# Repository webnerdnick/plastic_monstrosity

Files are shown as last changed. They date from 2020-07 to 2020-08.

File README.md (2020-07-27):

# Plastic Monstrosity
## 3D Printable 4' x 8' CNC machine

The printable part files are originally sourced from spiffcow's git repo, and details and documentation have been compied from the Thingiverse project page at: https://www.thingiverse.com/thing:2471313 and OpenBuilds here: https://openbuilds.com/builds/plastic-monstrosity.5353/

This repo was started as a way to further organize the project and make it easier for those wishing to build the project to understand how things come together. 

If you'd like to contact me with questions or contibuting, please feel free to contact me at webnerdnick@gmail.com.

### Original Summary of Project
> This is my massive CNC capable of cutting a full 4x8 sheet of plywood with room to spare! This is optimized specifically for cutting plywood, and I believe this is probably the least expensive way to build a CNC capable of accurately cutting plywood in a reasonable amount of time. There are other designs out there, but I've yet to see another one that maintains performance and accuracy while keeping the overall price below $1000 for a 4x8' cutting area. I really enjoyed designing and building this, and I hope it can help lower the barrier of entry for makers looking to build the kind of things you see on [OpenDesk](http://www.opendesk.cc) or [WikiHouse](https://wikihouse.cc/).

In a nutshell, this project uses 3D printable parts, tons of nuts and bolts, bearings, and some off the shelf parts from Open Builds, and 2" EMT conduit (or 60.3mmm conduit for European folks) for the long axis. For a complete listing of parts, please visit the BOM below.

While the short axis is primarily determined by the length of the C-Beam you purchase from OpenBuilds, the long axis can be nearly any length, if space is limited.

# Contents
[Bill of Materials](bom.md)

[Spindle Options](spindles.md)

[Print Settings](print_settings.md)

[Building the Table](building_bench.md)

[Adding the long-axis Rails (using the jig.stl)](adding_rails.md)

[Possible Upgrades](upgrades.md)

[FAQ](faq.md)

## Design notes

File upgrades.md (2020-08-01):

# Possible Upgrades

## OpenBuilds Short Axis Gantry Mount

The following upgrades will replace the 3D printed parts with machined plates and parts from OpenBuilds. This would allow for a much more rigid setup for attaching spindles, increasing overall accuracy.

This aassumes that you've already purchased the C-Beams, motor, and threaded rod for the z-axis, and have printed the endcap.stl, guardplate.stl, and the bottomEndcap.stl files.

*There are several nuts, bolts, and shims that need to be identified and added to the BOM below.*

| Qty. | Part | Price Ea. | Link |
|---|---|---|---|
| 2 | XLarge C Beam Gantry Plate | $14.99  | https://openbuildspartstore.com/xlarge |
| 1 | C-Beam Gantry Plate | $9.99 | https://openbuildspartstore.com/c-beam-gantry-plate/ |
| 1 | Motor Mount Plate - NEMA 23 | $7.99 | https://openbuildspartstore.com/motor-mount-plate-nema-23-stepper-motor/ |
| 8 | Solid V Wheel Kit * | $6.99 | https://openbuildspartstore.com/xtreme-solid-v-wheel-kit/ |
| 4 | 6mm Eccentric Spacer | $1.99 | https://openbuildspartstore.com/eccentric-spacer/ |

*Note: Requires Solid V Wheel kit, instead of Mini V Wheel kit for the gantry. 4 mini v wheels are still used for the z-axis plate.

Eccentric spacers should only be needed on the top side of the gantry in order to snug up the wheels.

From thingiverse, user Luk14, gave these overview pictures of his upgraded gantry, using the BOM above.

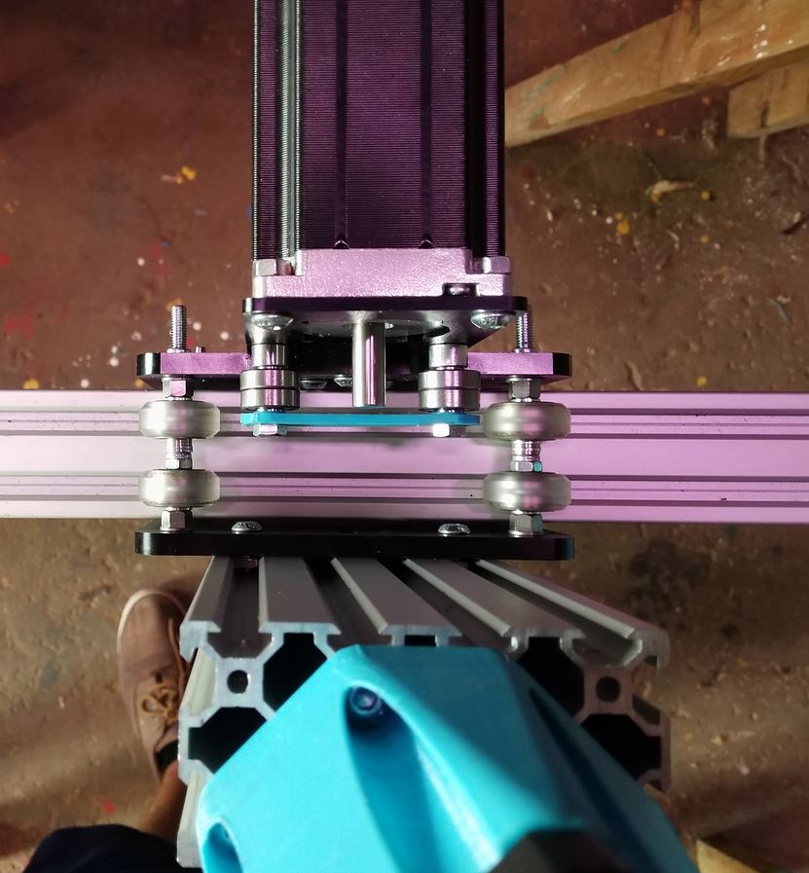
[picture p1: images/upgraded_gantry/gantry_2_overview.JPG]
upgraded gantry overview


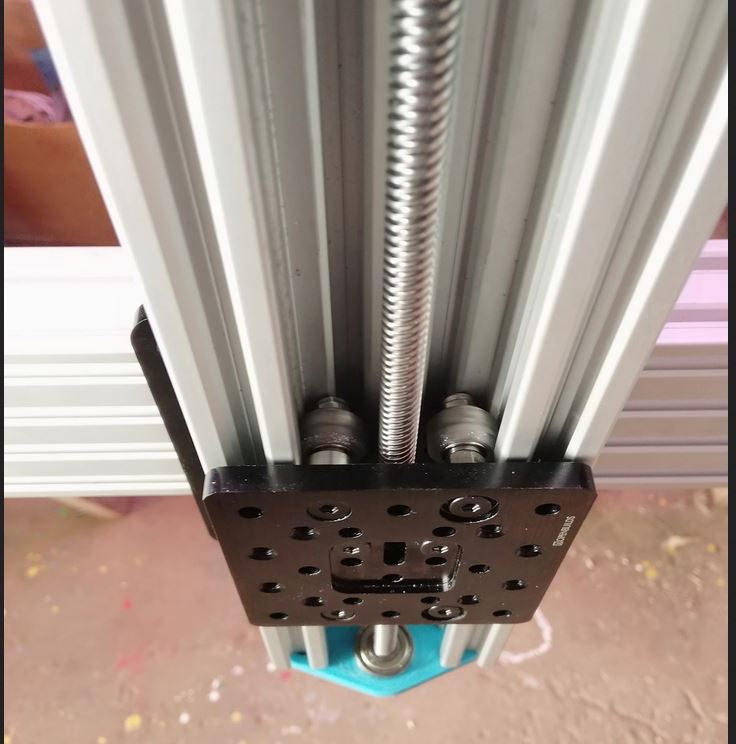
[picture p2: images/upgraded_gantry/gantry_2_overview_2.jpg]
upgraded gantry overview 2


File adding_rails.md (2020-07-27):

# Using to Jig to add rails to the workbench

Figure out how you're going to attach the conduit stand-offs to the condut. I'm using self-tapping screws, but I'll drill pilot hole in the conduit first using the jigs.  You can also get an M5 tap and a 4.5mm drill bit and make threaded holes. It's up to you, but before you do any drilling, figure out what you're going to attach the stand-offs with. You'll need something threaded so you can slightly adjust the stand-offs as you attach them at the end.

# Step 1
* Purchase two 10 foot pieces of 2" EMT conduit. It's metallic thin-wall conduit, and should be about 2-3/16" OD.
* Print 2 of the jig.stl files
    * Print using 20% infill out of PLA or something similar. These won't be used as part of the actual CNC machine, so it's ok to skimp here

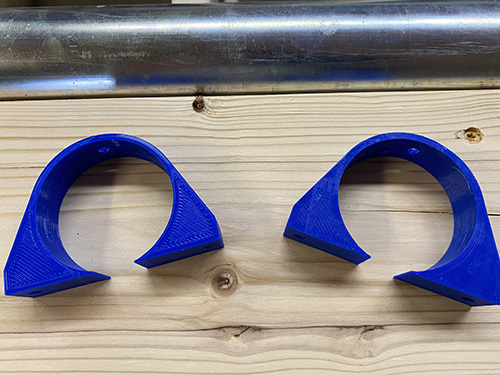
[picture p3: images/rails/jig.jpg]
jig templates


# Step 2
Using the jig, mark a line at 9' on the conduit, and cut at that length, it'll give you a nice line to follow when cutting with a hack saw or sawz-all

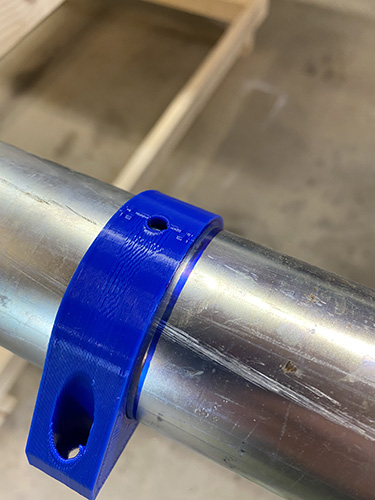
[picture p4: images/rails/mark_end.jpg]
marking the end


# Step 3
Using a file or sand paper, clean up the ends of the pipe, they'll be sharp

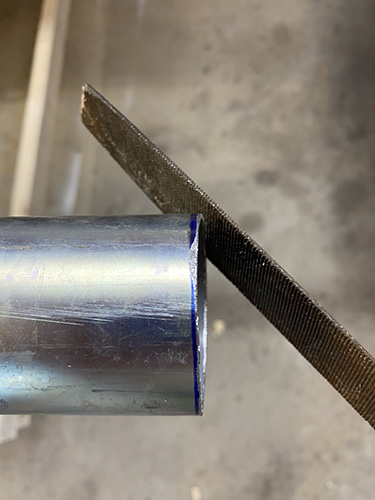
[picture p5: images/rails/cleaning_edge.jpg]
clean the end of the pipe


# Step 4
Most likely, you're conduit will have a slight bend along the length. Using a board with a flat edge, find the crown on the pipe by slowly rotating the pipe against the board. Note the opposite of the pipe where you have the greatest gap when laying up against the board.  This way when attaching your clips to the conduit, the can be parallel to the bend and make it easier to pull the bend out of the pipe as you screw it down to the workbench.

Here you can see this side of the pipe doesn't have a bend in it

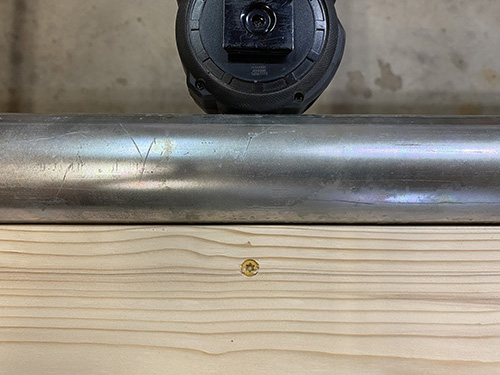
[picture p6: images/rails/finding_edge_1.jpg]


As I continued to rotate the pipe, this shows the crown, and I marked the opposite side

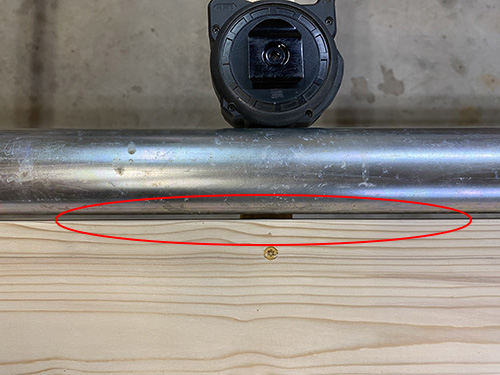
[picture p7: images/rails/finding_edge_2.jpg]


Here I marked 180 deg. from where the bend was the greatest against the straight edge. This point will become the side that I want to install the conduit mounts on.

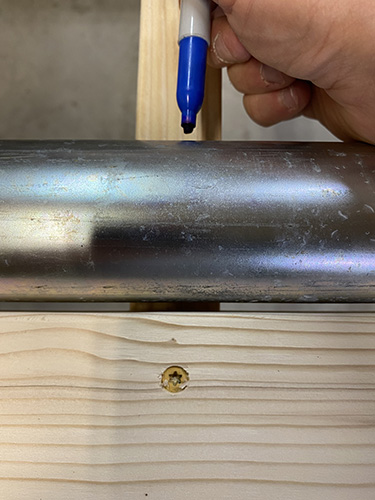
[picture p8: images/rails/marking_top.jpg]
making opposite side of bend


# Step 5
Let's put the jigs to use. Figure out how often you want to space the conduit stand-offs on the piece of pipe, you'll need to know that for buidling the jig.  I chose to space my stand-offs around 21".

On your flat board that you'll attach the jigs to, measure the distance you want to space the jigs and make a mark on the board.  

Slide your jigs over the conduit, and place them on the marks you made on the board.  Right now, spacing on the pipe itself it's important, we're just focusing on attaching the jigs to the board, and the pipe is there to make sure they are lighed up properly. Screw the jigs down to the board at the spacing you set.  One side can be screwed down tight, but leave a few turns left when you screw down the other side of the jig. This will allow the pipe to slide.

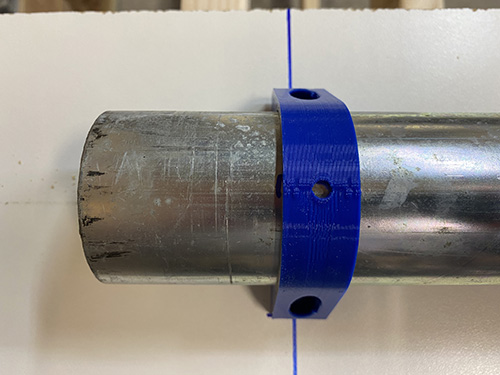
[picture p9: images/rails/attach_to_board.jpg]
space the rails


# Step 6
I left 2" at the end of the pipe before drilling a hole for the first conduit stand-off. You'll need to leave yourself some space for the long-axis belt mount.

Rotate your pipe, so the mark you made on the crown is up.

Mark or drill the first hole in the conduit using the top hole in the jig.

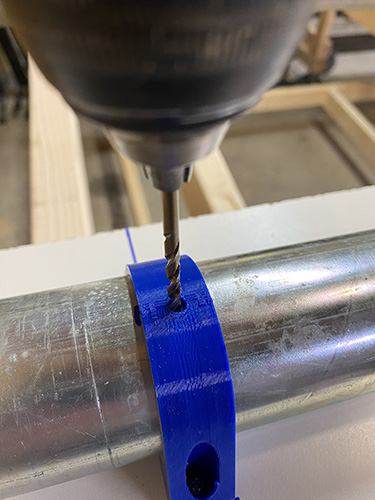
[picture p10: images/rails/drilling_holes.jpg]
drill holes


# Step 7
After drilling one hole, place a screw, bolt, or spare drill bit into the hole, so the pipe doesn't move, and drill the second hole using the other jig.

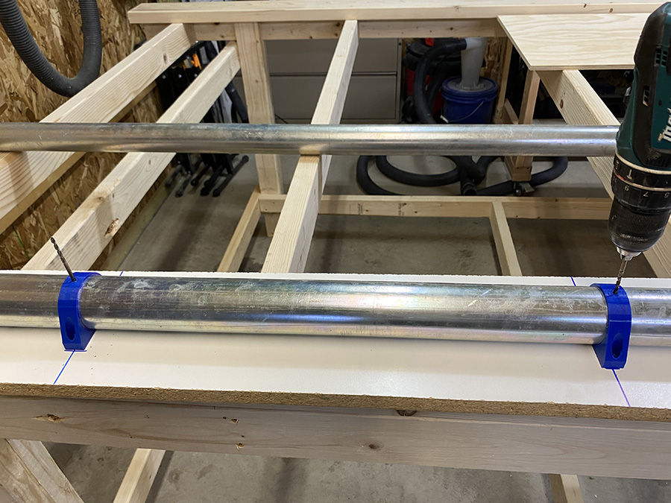
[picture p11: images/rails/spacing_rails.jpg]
drill 2nd hole


# Step 8
Once you drill the 2nd hole, remove the drill bit in the first hole, and slide the pipe down through the jigs so that the 2nd hole now lines up with the hole in the first jig, and put another drill bit or something in that hole to keep the pipe from turning.  

Now drill another hole using the 2nd jig.

Repeat until you reach the end of the pipe.

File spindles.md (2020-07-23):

# Spindle Options

Depending on the rigidity of the short-axis gantry, your options could almost be limitless. However, with 3D printed parts, the following options are recommended.

## Makita RT0701c 1-1/4 HP Compact Router

* 1/4" Collet
* Broad RPM range or 10,000 to 30,000 RPM
* Easy to replace brushes and bearings
* About 4 lbs
* Around $99 on [Amazon](https://www.amazon.com/gp/product/B00E7D3V4S)

*Use the makita.stl part to hold this spindle*

## Dewalt DWP611 1-1/4 HP Router
* 1/4" Collet
* 16,000 - 27,000 RPM
* LED Work Light
* About 5 lbs
* Around $139.00 on [Amazon](https://www.amazon.com/gp/product/B0048EFUV8)

*Use the dwp611.stl to hold this spindle*

## Carbide Compact Router
* 110 V AC only with US Plug
* 1/4" Collet
* 12,000 - 30,000 RPM
* Rebranded Makita
* 14 foot power cord
* comes with 2 sets of replacement brushes
* $80 at [Carbide3D](https://shop.carbide3d.com/products/carbide-compact-router?variant=14063567667261)

*Use the zAxis_65mm_spindle.stl to hold this spindle*

## Generic Options

52mm, 70mm, and 80mm generic spindle mounts are also included in the printable parts, for a range of other available spindles. I do not have any specific experience or recomendations for a generic spindle.

*Use zAxis-52mm-spindle.stl, zAxis-70mm-spindle.stl, or zAxis-80mm-spindle.stl

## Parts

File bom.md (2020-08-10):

# Bill of Materials

I'm doing my best to provide a complete bill of materials with complete sources. During certain times, specifically linked items may be out of stock, but as long as you substitute with an equivalent item, you should be ok. I am continually updating this list.

All sources and prices below are accurate of 7/23/2020, prices and availability may fluctute. All sources are for USA shipping.  

*If anyone would like to research and provide me with reasonable substitutions or links for other countries, please reach out to me.*

## Electronics

| Qty.  | Item | Price Ea.  | Site | Link | Comments |
| ----- | --- | --- | --- | -----| --- |
| 1 | MKS Sbase Board | $53.99 | Amazon | https://www.amazon.com/gp/product/B071X8MBYT/ref=crt_ewc_img_dp_3?ie=UTF8&psc=1&smid=A2K1WYI5NZ8QSW | Main controller board|
| 1 | 24V DC 15A 360W PSU | $18.98 | Amazon | https://www.amazon.com/gp/product/B0146IAXYO/ref=crt_ewc_img_dp_4?ie=UTF8&psc=1&smid=AMNTPWSAB5H0S | Primary PSU|
| 3 | NEMA 23 Stepper Motor 269 oz/in, 76cm, **8mm bore** | $28.00 | Amazon | https://www.amazon.com/gp/product/B07Y81FF3V/ref=crt_ewc_img_dp_2?ie=UTF8&psc=1&smid=A1AY59LT54ZBYI | Long and Short Axis Motors |
| 1 | NEMA 17 Stepper Motor, 84 oz/in 48mm body | $13.99 | Amazon | https://www.amazon.com/gp/product/B00PNEQKC0/ref=crt_ewc_title_dp_7?ie=UTF8&psc=1&smid=AWQBCGWISS7BL | z-axis motor |
| 1 | 100 ft 18/4 stranded wire ** | $28.78 | Amazon | https://www.amazon.com/gp/product/B01KWBPC6S/ref=crt_ewc_title_dp_2?ie=UTF8&psc=1&smid=A23GDHUTXWRYW4 | |
| 1 | JST SM Connectors (600qty male/female) ** | $15.99 | Amazon | https://www.amazon.com/gp/product/B074LVGVTY/ref=crt_ewc_title_huc_3?ie=UTF8&psc=1&smid=A6QA7SV6MW7GH | For connecting steppers to CPU|

***You're not going to need all 600 of these connectors, you'll only need a handful to make extension cables for the stepper motors
to connect to the controller board. The stepper motors DO NOT come with plugs or long cables.

Also, 18 AWG wire is the smallest wire recommended (bigger the number, smaller the wire dia.), make sure you're purchasing stranded wire as well*

## Rails and Conduit

| Qty.  | Item | Price Ea.  | Site | Link | Comments |
| ----- | --- | --- | --- | -----| --- |
| 2 | 2" EMT (thin wall) electrical conduit. NOT PVC  | $26.99 | Ace Hardware | | Outside dia. is 2-3/16"|
| 1 | C-Beam Linear Rail, 1500mm (59") | $47.99 | Open Builds | https://openbuildspartstore.com/c-beam-linear-rail/ | Short Axis|
| 1 | C-Beam Linear Rail, 250mm (9.8") | $8.99 | Open Builds | https://openbuildspartstore.com/c-beam-linear-rail/ | z-axis |

# Moving Things

| Qty.  | Item | Price Ea.  | Site | Link | Comments |
| ----- | --- | --- | --- | -----| --- |
| 2 | 5 meter Timing Belt, 10mm Wide, 2mm Pitch | $13.98 | Amazon | https://www.amazon.com/gp/product/B078STSGSX/ref=crt_ewc_img_dp_8?ie=UTF8&psc=1&smid=A3CUHW0VYGYSCN |  long and short axis|
| 1 | 300 mm T8 Lead Screw, 2mm pitch, 2 start 4mm lead | $9.99 | Amazon | https://www.amazon.com/gp/product/B07ZC741KB/ref=ppx_yo_dt_b_asin_title_o00_s00?ie=UTF8&psc=1 | z-axis|
| 1 | 5 pack 2GT-20 Timing Pulley, 20 teeth, 10mm width, 8mm bore ** | $10.99 | Amazon |  https://www.amazon.com/gp/product/B079JMHZW7/ref=crt_ewc_img_srh_1?ie=UTF8&psc=1&smid=A31QZVWR40HWH8 ||
| 1 | 4 pack 5mm to 8mm leadscrew coupler | $6.99 | Amazon | https://www.amazon.com/KINGPRINT-Coupling-Accessories-Engraving-Machines/dp/B073FDXHMG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 | coupling z-axis motor to leadscrew |
| 1 | 20 pack 625-zz bearing (5mm x 16mm x 5mm) | $9.95 | eBay | https://www.ebay.com/itm/625-ZZ-C3-Premium-Metal-Shielded-Ball-Bearing-5x16x5-625Z-20-QTY/303360064601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 | |
| 1 | 2- Pack 608-zz bearings (8mm x 22mm x 7mm) | $8.99 | Amazon | https://www.amazon.com/gp/product/B07211VH78/ ||
| 12 | Xtreme Mini V Wheel Kit *** | $5.99 | Open Builds | https://openbuildspartstore.com/xtreme-mini-v-wheel-kit/ | short and z-axis wheels |

***The bore must match whatever shaft diameter is on your NEMA 23 motors. The more popular 6.35mm x 10mm wide pulleys were impossible to find, so I changed out my steppers to an 8mm bore, along with these pulleys.  Pay careful attention to the specs of the pulley. 20 teeth, 10mm wide.
****If you plan to use the upgrade of the Open Builds short axis gantry, you only need 4 Xtreme Mini V Wheels instead of 12, as you'll then need 8 Solid V wheels. (See [upgrades](upgrades.md) for BOM)*

# Nuts and Bolts

Out of convenience and better pricing, large packs of nuts and bolts are linked, though you may not need 50 of one thing, it'll still be cheaper than having to buy 30 at a local store. YMMV. I've tried to actualy list how many of each you'll actually use in case you want to get them locally.

*Note: Consider stainless steel or zinc options if your CNC machine will be exposed to humidity or stored in a garage or shed*

| Qty.  | Item | # Used | Price Ea.  | Site | Link | Comments |
| ----- | --- | ---|--- | --- | -----| --- |
| 1 | Anti-Backlash Nut, 8mm T8, 4mm Lead | 1 | $8.88 | Amazon | https://www.amazon.com/gp/product/B07T2MYS6D/ref=crt_ewc_title_dp_5?ie=UTF8&psc=1&smid=A3C0HXP4AGBIOG | |
| 1 | 100 pack m5 lock nut 0.80 thread | | $8.94 | eBay | https://www.ebay.com/itm/Stainless-Steel-Nylon-Insert-Hex-Lock-Nut-M2-5-M3-M4-M5-M6-M8-M10-M12-DIN-985/122599345751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 | |
| 1 | 50 pack m5 THIN jam nuts, 0.80 thread | | $13.99 | eBay | https://www.ebay.com/itm/Metric-DIN-439B-Jam-Nuts-Zinc-Plated-Steel-Class-04-Jam-Thin-Hex-Nuts-M4-M36/401806123372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 | |
| 3 | 50 pack 20 series m5 Tee Nut, Slide-In  ** | | $8.99 | Amazon | https://www.amazon.com/gp/product/B07MHH1HFQ | |
| 1 | 20 pack m5 75mm cap head bolt | | $9.61 | eBay | https://www.ebay.com/itm/M5-Socket-Head-Cap-Screws-12-9-Alloy-Steel-w-Black-Oxide-DIN-912-0-80-Coarse/112016494139 | |
| 1 | 50 pack m5 30mm cap head bolt | | $9.30 | eBay | https://www.ebay.com/itm/M5-Socket-Head-Cap-Screws-12-9-Alloy-Steel-w-Black-Oxide-DIN-912-0-80-Coarse/112016494139 | |
| 1 | 50 pack m5 25mm cap head bolt | | $8.45 | eBay | https://www.ebay.com/itm/M5-Socket-Head-Cap-Screws-12-9-Alloy-Steel-w-Black-Oxide-DIN-912-0-80-Coarse/112016494139 | |
| 1 | 100 pack m5 12mm cap head bolt | | $11.72 | eBay | https://www.ebay.com/itm/M5-Socket-Head-Cap-Screws-12-9-Alloy-Steel-w-Black-Oxide-DIN-912-0-80-Coarse/112016494139 | |
| 20 | 5/16"-18 lock nuts (nylon) | | $0.15 | Ace Hardware | | used on long axis |
| 4 | 5/16"-18 Hex bolt 2" long | | | Ace Hardware | | long axis, center bearings |
| 10 | 5/16"-18 hex bolt 3.5" long  ****** | | $0.45 | Ace Hardware | | used on long axis | 
| 20 | 5/16"-18 hex bolts 1.5" long | | $0.25 | Ace Hardware | | long axis, side bearings |

***You want slide-in, NOT drop-in tee nuts. The drop in are a pain to work with, but make sure you have the right amount of nuts in the slot before assembling or you'll have to take it apart to add a nut*

*******These may not be needed, currently in review.*

# Cutting Things 
| Qty.  | Item | Price Ea.  | Site | Link | Comments |
| ----- | --- | --- | --- | -----| --- |
| | Makita Compact Router | $99.00 | Amazon | https://www.amazon.com/gp/product/B00E7D3V4S | |
|  OR  | |||||
| | DeWalt DWP611 Router | $139.00 | Amazon | https://www.amazon.com/gp/product/B0048EFUV8 | |
| | | | | | |
| 1 | 1/4" Up-Cut Solid Carbide Spiral Bit ** | $19.53 | Amazon | https://www.amazon.com/gp/product/B000K2BGNS | |

***Lowes also carries these, but they are about $2-$3 more expensive than Amazon.*

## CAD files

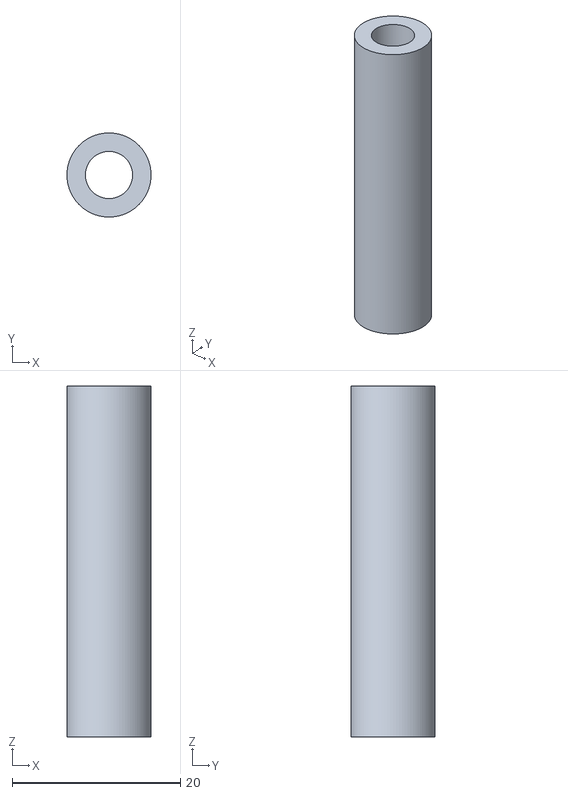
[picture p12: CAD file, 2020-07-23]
part_files/shortAxisFullLengthSpacer.stl
10.0 x 9.99 x 41.7

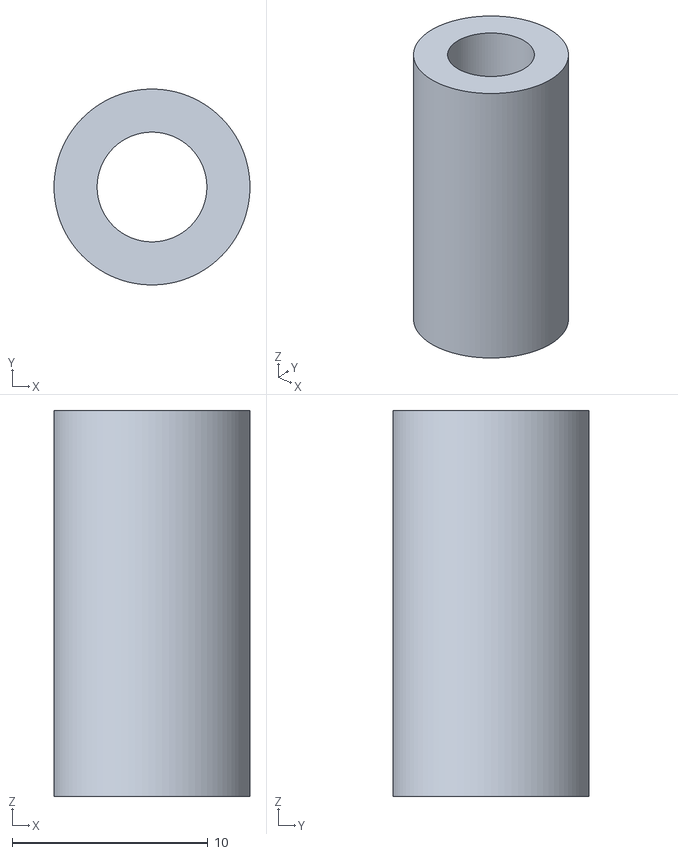
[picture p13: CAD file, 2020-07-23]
part_files/official/longAxisFullLengthSpacer.stl
10.0 x 9.99 x 19.7

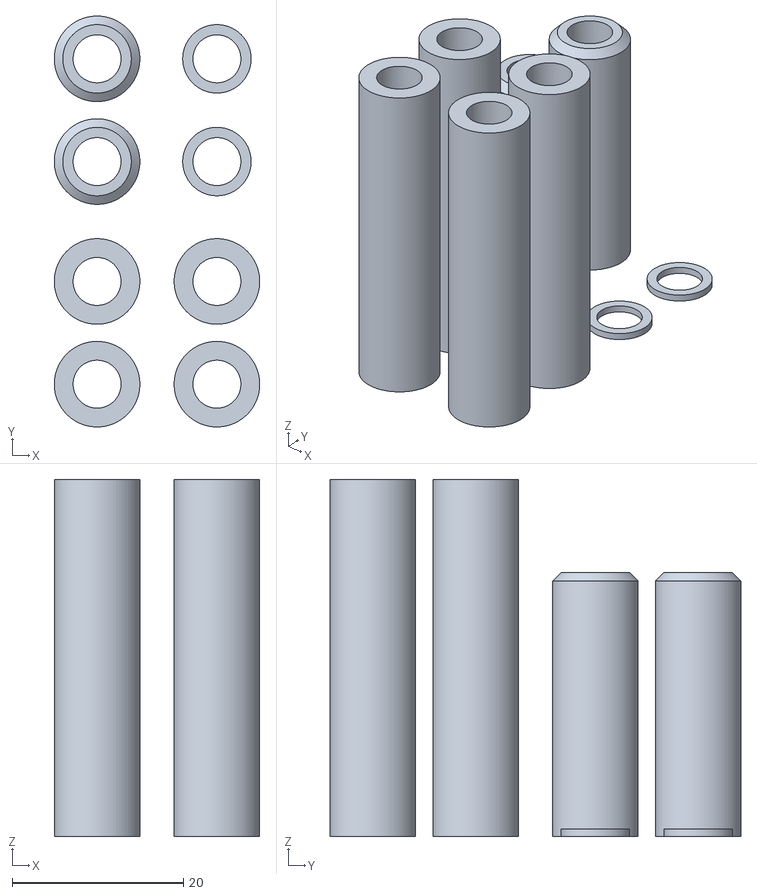
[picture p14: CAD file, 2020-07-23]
part_files/official/2017-08-07/shortAxisSpacers.stl
24.0 x 48.0 x 41.7

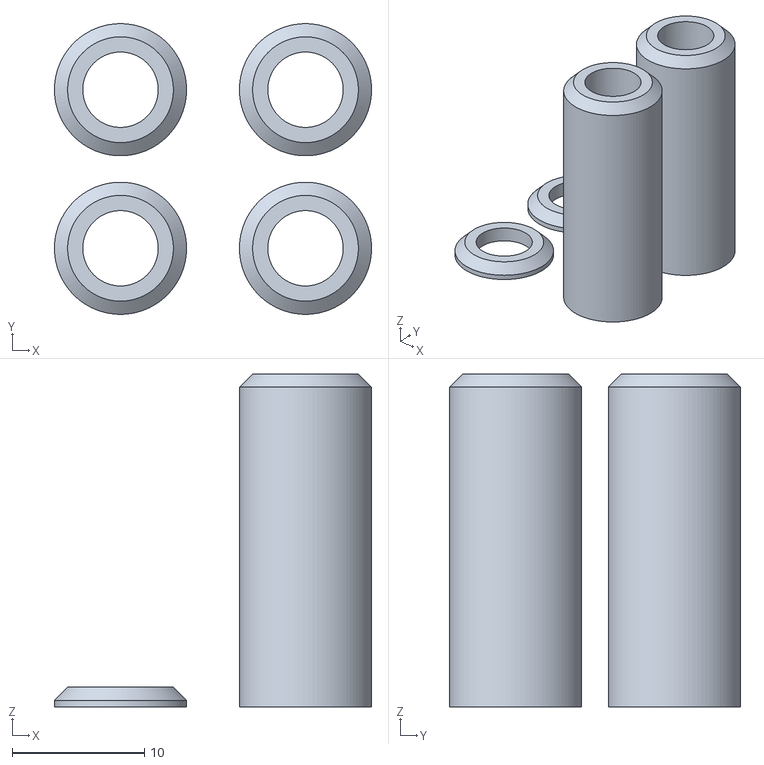
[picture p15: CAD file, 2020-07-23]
part_files/official/2017-08-09/shortAxisSpacers_bearingonly_shortMotorShaft.stl
24.0 x 22.0 x 25.2

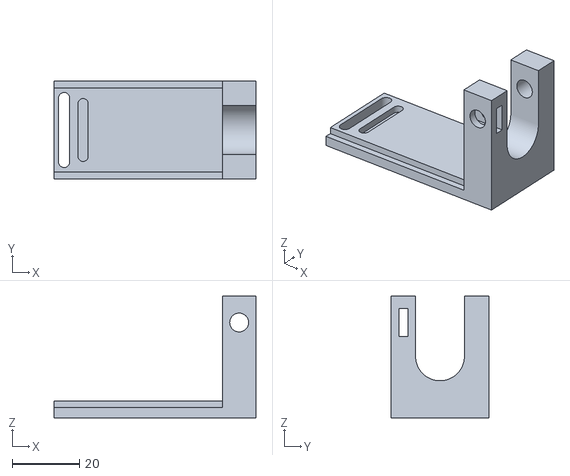
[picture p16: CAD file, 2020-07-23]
part_files/official/2017-08-16/probeHolder.stl
60.0 x 29.0 x 36.1

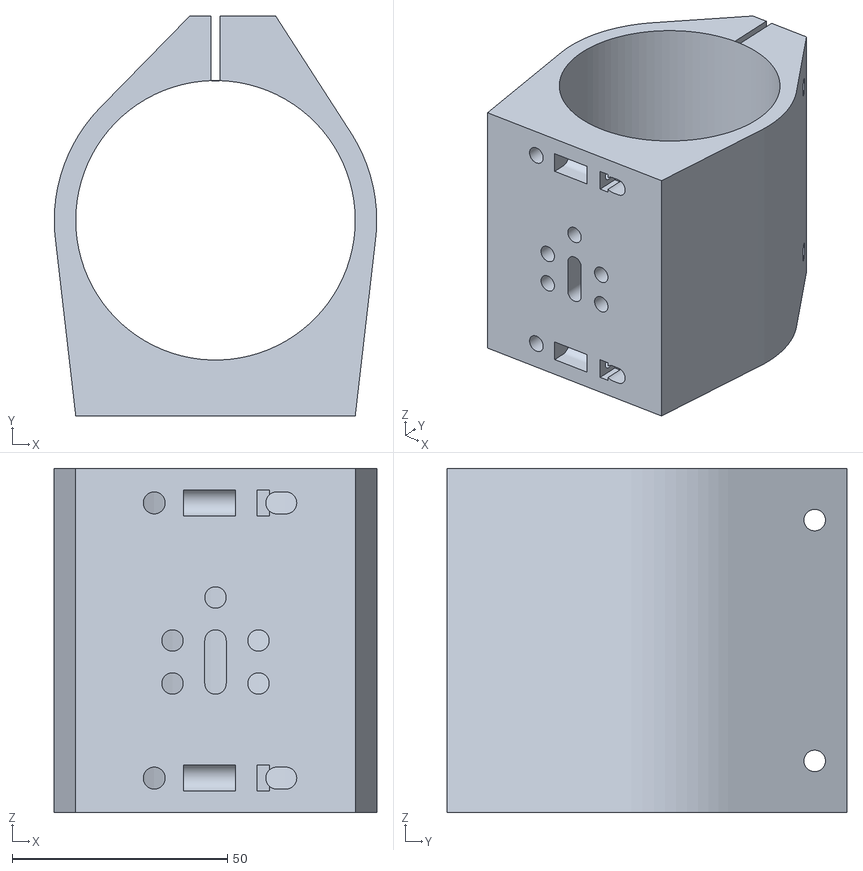
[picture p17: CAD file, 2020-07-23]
part_files/official/2017-08-22/makita.stl
75.0 x 93.0 x 80.0

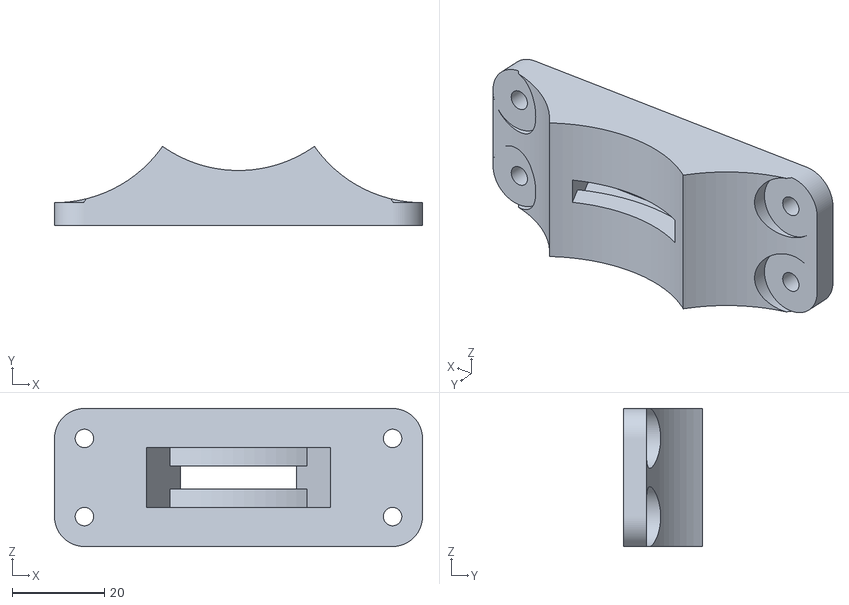
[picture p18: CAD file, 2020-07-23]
part_files/official/2017-09-20/ConduitUndersideBase_60.3mm.stl
80.0 x 17.3 x 30.0

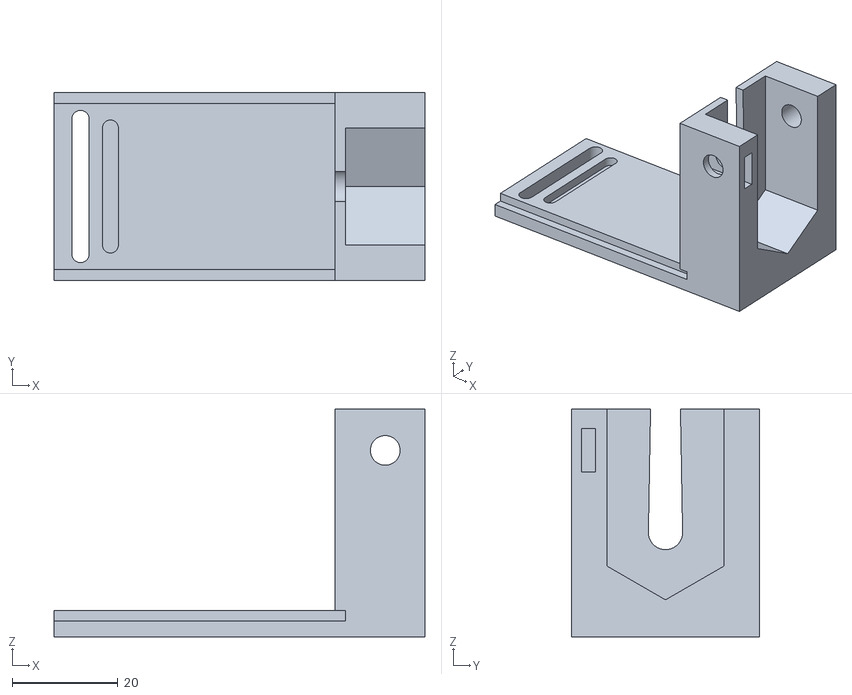
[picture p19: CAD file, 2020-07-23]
part_files/official/2017-10-05/probeHolder-Makita.stl
70.0 x 35.4 x 43.0

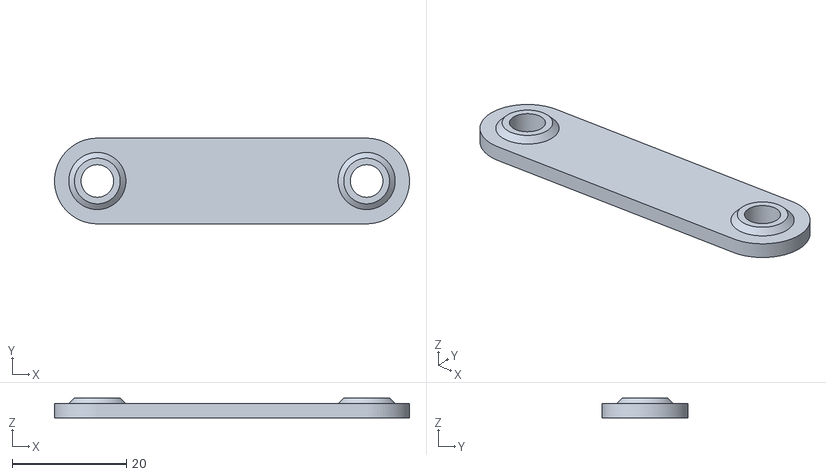
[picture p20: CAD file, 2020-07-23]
part_files/official/2017-11-02/guardPlate.stl
62.1 x 15.0 x 3.50

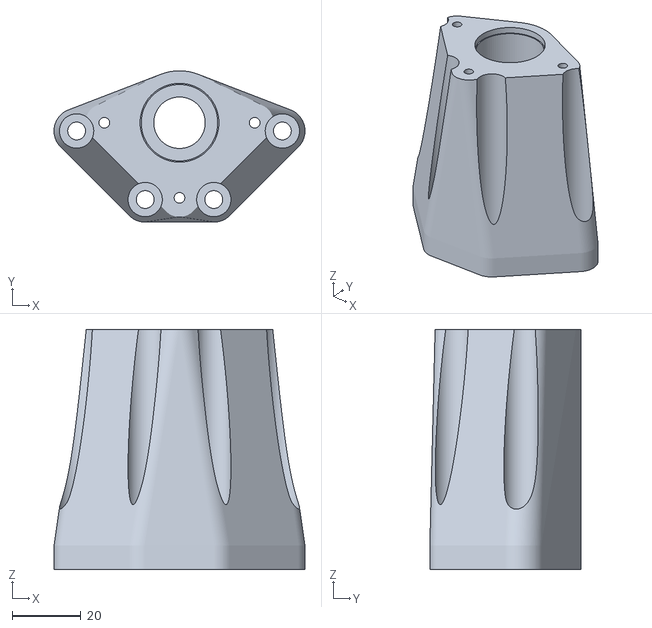
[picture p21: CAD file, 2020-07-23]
part_files/official/2017-12-03/endcap.stl
73.2 x 44.1 x 70.0

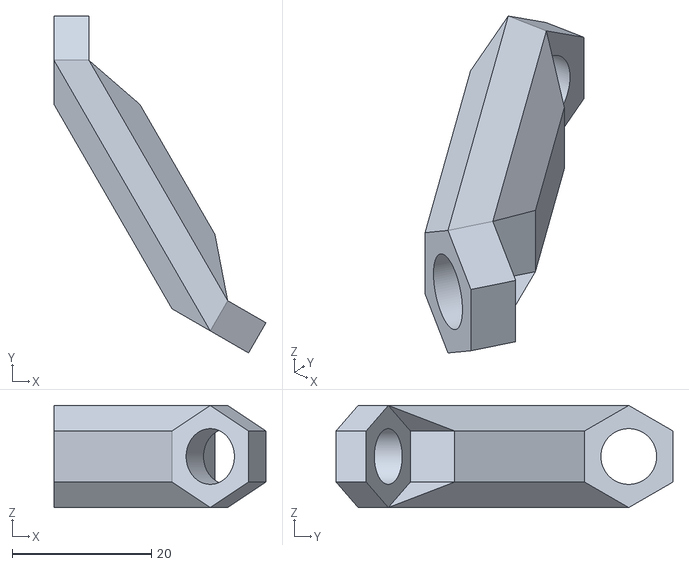
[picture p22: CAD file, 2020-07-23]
part_files/official/brace.stl
30.4 x 48.4 x 14.7

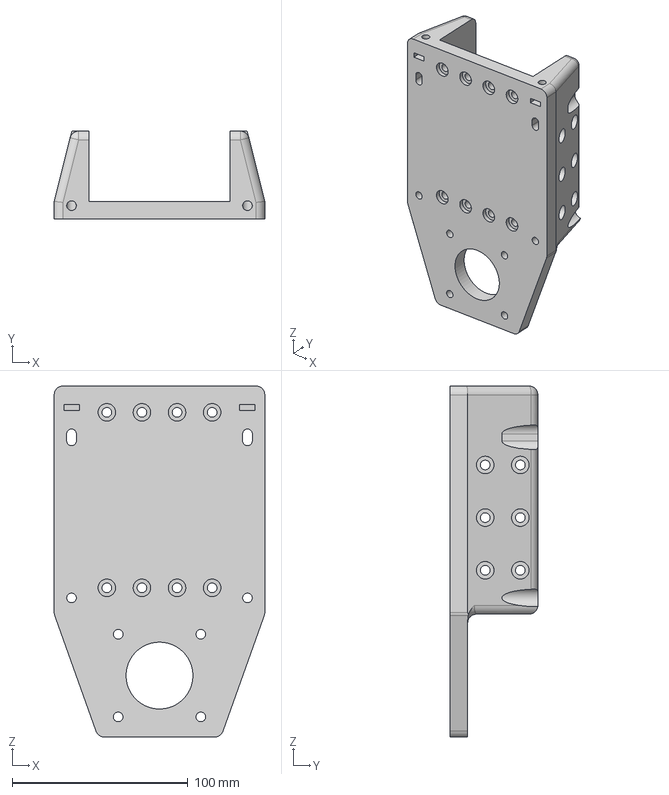
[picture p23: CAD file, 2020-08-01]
part_files/redesigned/shortAxisPlateFront.step
120.0 x 50.0 x 200.0 mm

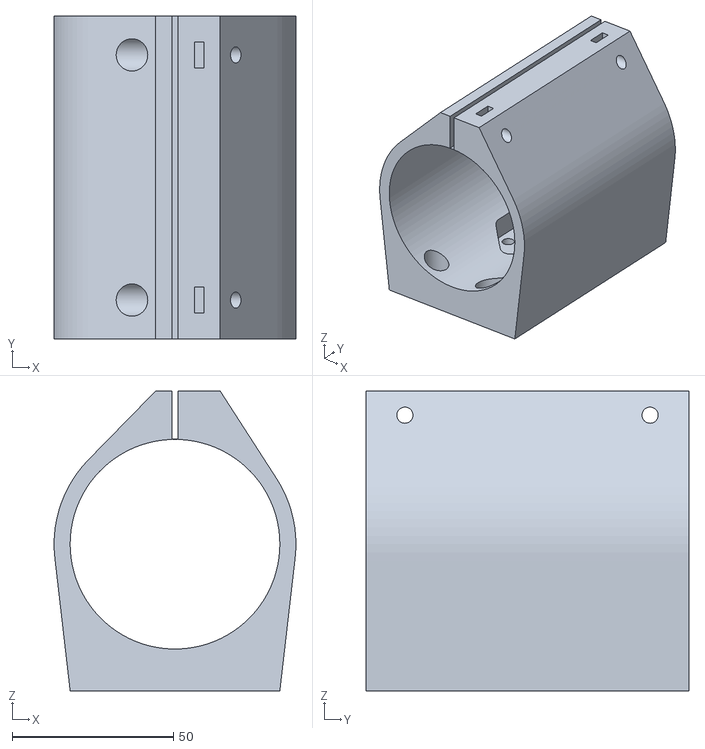
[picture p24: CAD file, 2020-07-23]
part_files/zAxis_65mm_spindle.stl
75.0 x 100.0 x 93.0

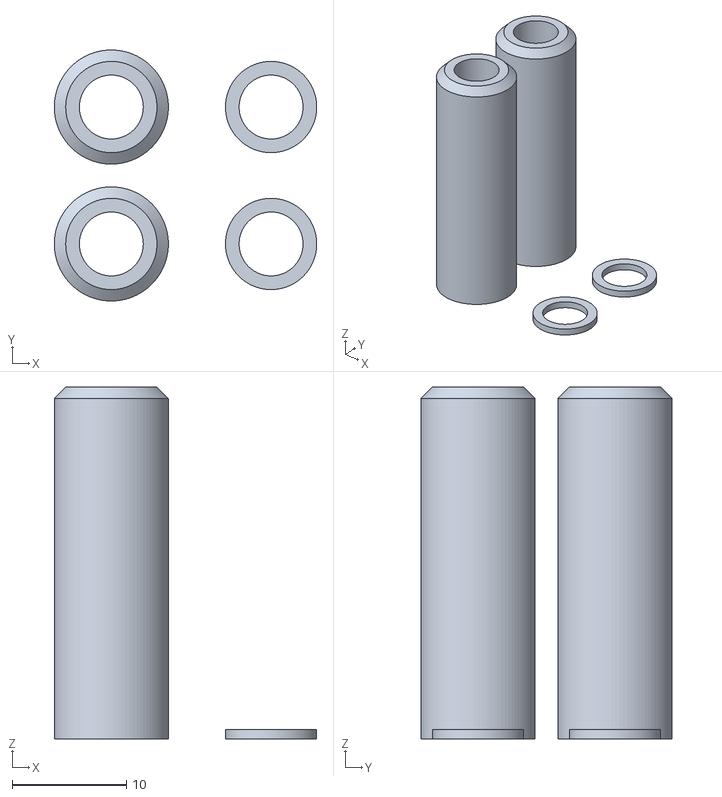
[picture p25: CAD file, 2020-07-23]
part_files/official/2017-08-07/shortAxisSpacers_bearingonly.stl
23.0 x 22.0 x 30.9

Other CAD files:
part_files/official/2017-08-09/beltMountShortAxis_shortMotorShaft.stl
part_files/official/2017-08-22/dwp611.stl
part_files/constants.scad
part_files/beltMount.scad
part_files/beltMount_60.3mm.scad
part_files/beltMountShortAxis.scad
part_files/20mm_spacer.stl
part_files/625Spacer.stl
part_files/6mm_spacer.stl
part_files/Carriage.scad
part_files/Carriage2.scad
part_files/Carriage3.scad
part_files/Carriage3_20.4mm.scad
part_files/Carriage3_60.3mm.scad
part_files/Carriage3_test.stl
part_files/Carriage4.scad
part_files/UAE8-to-5mm.scad
part_files/UAE8-to-5mm.stl
part_files/beltMount.stl
part_files/beltMountShortAxis.stl
part_files/beltMountShortAxis_shortShaft.scad
part_files/beltMountShortAxis_shortShaft2.scad
part_files/beltMountShortAxis_shortShaft3.scad
part_files/bottomEndcap.stl
part_files/brace.scad
part_files/carriageSpacer.stl
part_files/connector.scad
part_files/connector.stl
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

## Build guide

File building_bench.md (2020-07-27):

# Building the Bench

Your new Plastic Monstrosity needs something to live on, so this is where we discuss what the table should look like.  Tables and work benches can be made hundreds of different ways, and I'll outline a simple build process for the most basic of tables on which to mount your Monstrosity.

Everyones range of build experience is going to differ here, but at a minimum, since you're attempting to build this monstrosity in the first place, I'll assume you at least have some sort of basic building skills.  For simplicity sake, we'll build a workbench out of 2x4 and 2x6 lumber.

## Basic Requirements

* Simple to build using home-center products (2x4 and 2x6 standard lumber)
* Rigid and built to withstand racking
* Not too heavy to move or properly level
* Able to support full-sheet (4'x8') material

### Where to get stuff
Lowes and Home Depot are going to be your best resources here for the obvious things like lumber, and support braces.

Check places for Amazon for things like leveling feet, or lockable casters if you want to move the monstrosity around.

Some ideas to get you started:

* [4" Heavy Duty Casters with Leveling Feet](https://www.amazon.com/SPACECARE-360-Degree-Polyurethane-Adjustable-Leveling/dp/B07RDPSNYR/)
* [2" Locking Swivel Casters](https://www.amazon.com/Swivel-Caster-Wheels-Locking-Polyurethane/dp/B06Y49D2J2/)
* [Leveling Feet](https://www.amazon.com/Adjustable-Furniture-Levelers-Shelving-Cabinets/dp/B06ZXSXL5Z)

## The Design

I got the basic idea from Kreg tool for these workbench plans: https://www.buildsomething.com/plans/P615A51E86DAF5AD5/DIYWorkbench though I've designed several other workbenches in the past on my own.

You can use the above guide and expand it to fit the plastic monstrosity.  We're aiming for about 5'-6" wide by 9' long, and 38" high is a good height for me, but pick something that works for you.

> Overall table size should be around 5-6" x 9' (66" wide by 108" long)

The original creator used a workbench made out of 2x6 material and simpson strongties from Home Depot, but we're going to simplify the design a little.
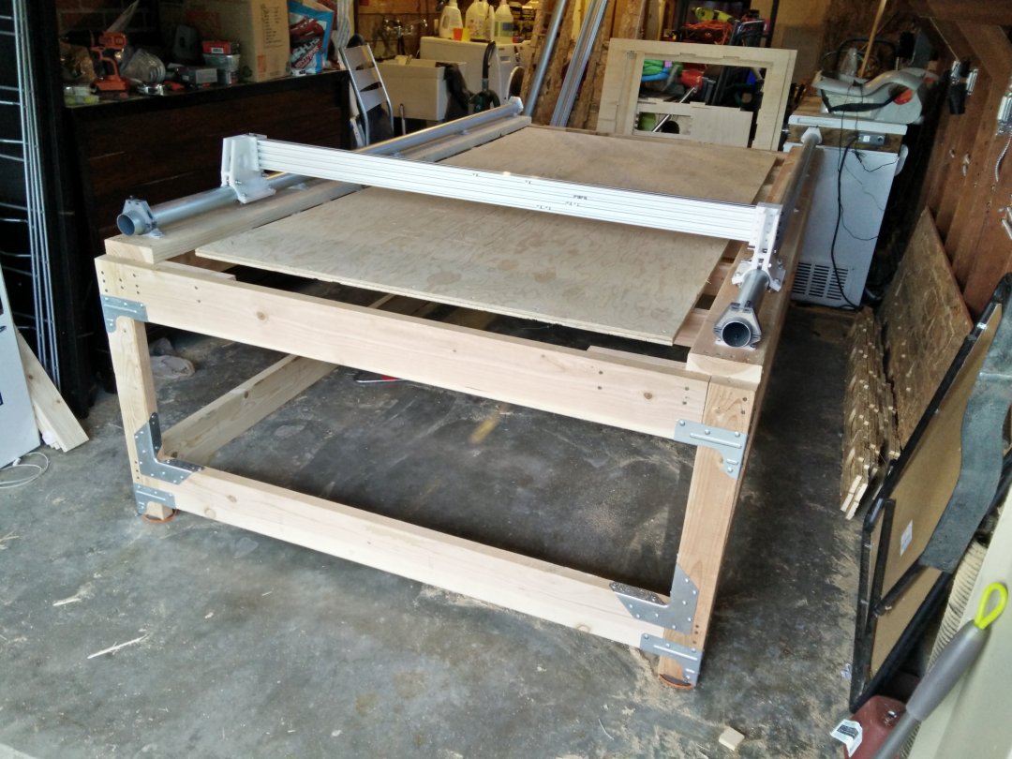
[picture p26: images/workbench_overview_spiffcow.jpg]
spiff cows workbench


## Step 1
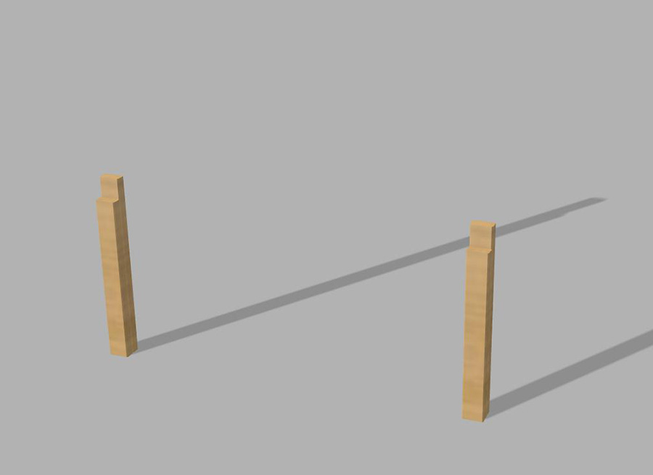
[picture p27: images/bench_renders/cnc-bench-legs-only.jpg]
cut legs


Cut list:

For a 38" high bench, you'll need to make **4 of the following legs**:
* 1x 38" long (or however high you want your bench to be) 2x4 
* 1x 34-1/2" long (3-1/2" shorter than the bench height) 2x4

Nail the shorter piece to the front of the longer piece, with the bottoms being flush

## Step 2
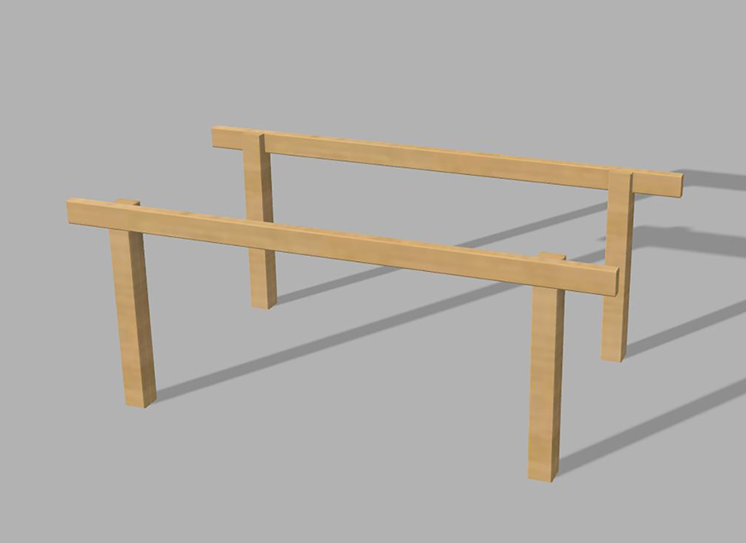
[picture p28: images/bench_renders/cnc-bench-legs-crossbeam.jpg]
bench legs crossmember


Cut List:

If you are making a full-sheet length CNC machine, you'll want you bench to be 9' (108") long

* 2x  108" long 2x4

Attach your long board into the notch that was created by the legs. I placed my legs 14" in from either side on the board.

## Step 3
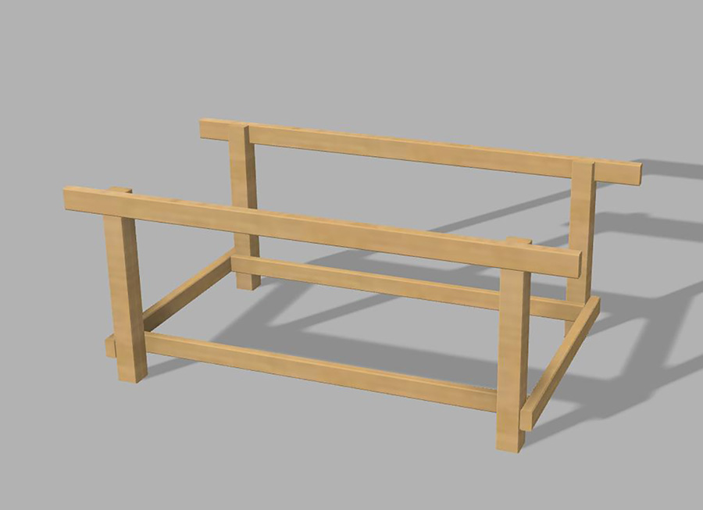
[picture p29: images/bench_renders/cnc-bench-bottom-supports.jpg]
bench bottom supports


Cut List:

* 2x 66" long 2x4 (this will be the maximum width of the table)
* 2x 80" long 2x4 (bottom support)

Attach your 66" board across the 2 sets of bench uprights you created in step 2. Put it about 6" off the floor, and attach it so the outer edges are flush with the outer edges of the legs.

Take the 80" long board and attach it inside the legs, flush with the back of the other support board you just added

## Step 4
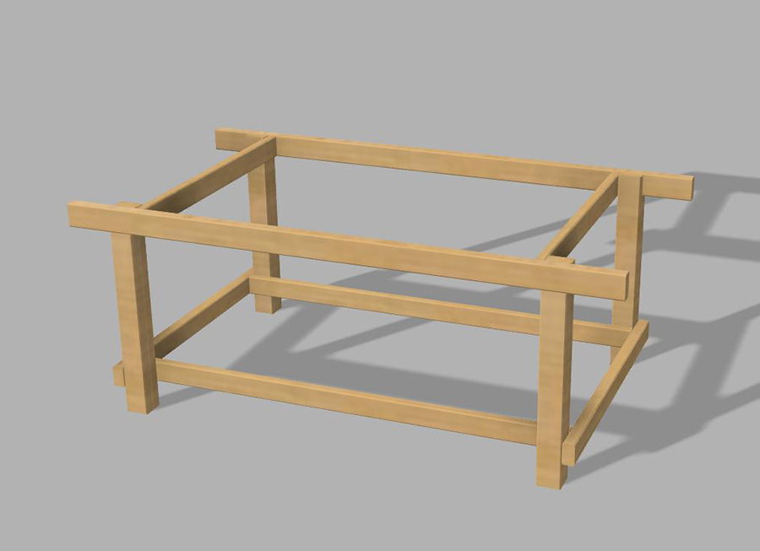
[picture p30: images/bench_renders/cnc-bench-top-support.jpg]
bench top supports


Cut List:
* 2x 63" long 2x4 (the width of your table from step 3, minus 3")

Attach these boards at the top inside of the legs, use a level to make your uprights plumb.

## Step 5
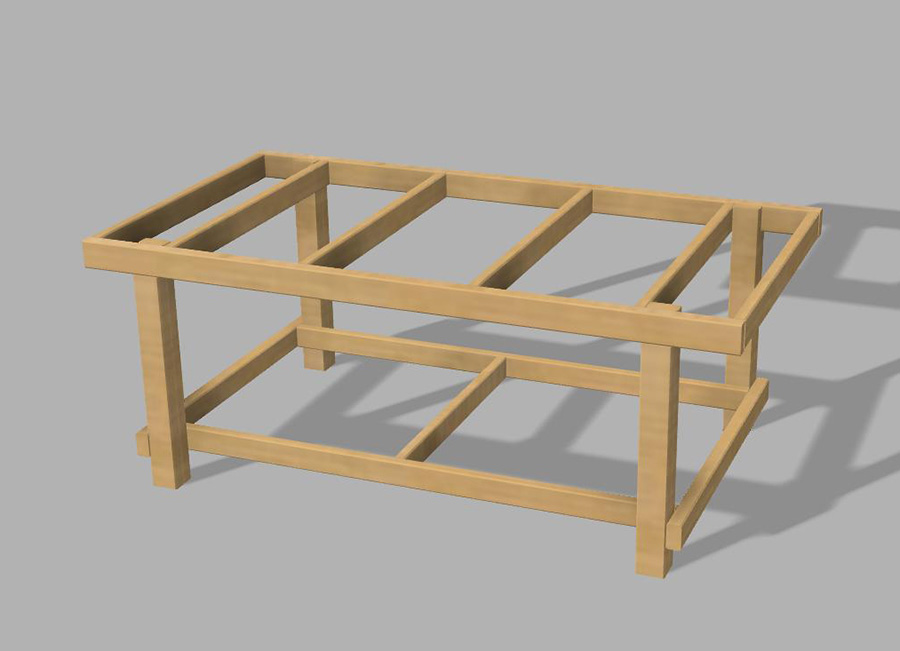
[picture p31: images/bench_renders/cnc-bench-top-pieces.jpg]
bench material support pieces


Cut List: 
*4x 63" long 2x4s
*1x 57" long 2x4

These will be part of your material supports, place one at each end of the bench, and space the others evenly across the length of the bench.  You can make more if you want more support for whatever material you are cutting.

Take the 57" long 2x4 and use it to stretch across the bottom supports in the middle to stabalize those supports

## Step 6
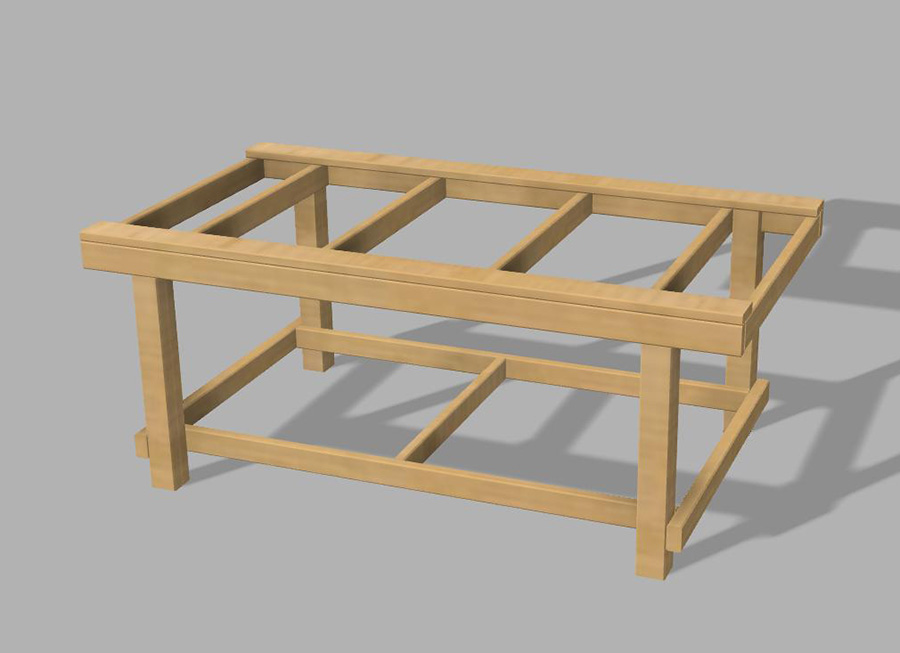
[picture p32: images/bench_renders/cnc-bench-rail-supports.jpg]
bench rail supports


Cut List:
* 2x 108" long 2x6 (or whowever long you made your bench)

This is the support for your long-axis rails. Attach either 2x6 to the top of the bench, flush to the outer sides, and flush with the long horizontail rails.

## Completed Bench
*shown with long-axis EMT conduit

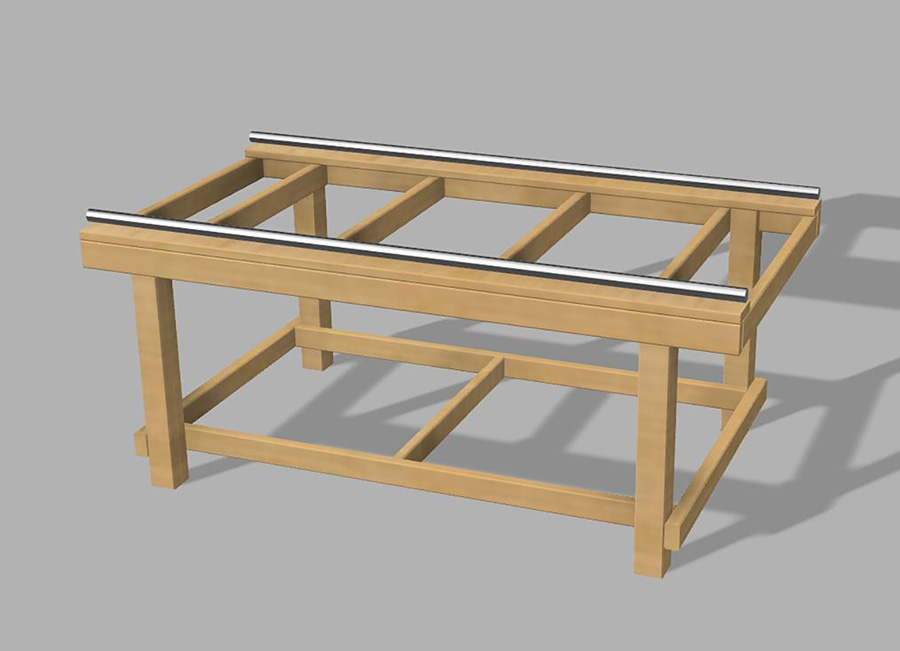
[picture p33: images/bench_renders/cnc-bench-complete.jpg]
completed bench


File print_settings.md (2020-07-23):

# Print Settings
The files provided here are intended for printing on a 3D FDM printer, like the Creality Ender 3, Prusa3D I3 MK3S, or similar brands.  A reasonable accuracy and resolution is required to build parts for accurate CNC cuts.

*Note: Some gantry pieces can be substituted using parts from OpenBuilds instead of 3D printing. Please visit the Possible Upgrades section.*

## Recommended Material

* High quality PETG is recommended over anything else
* PLA+/PLA Pro from brands like Atomic Filament or eSun would work as a good substitution with higher-infill
* Not recommended: Regular PLA, as it'll break down over time and you may experience issues with layer separation

## Infill

50% or higher. I printed my parts in eSun PLA+ with 55% infill

*Note: some parts like the Jig, and possibly the conduit supports can be printed with 20-25% infill

## Print Notes

* Print with high temps for good layer bonding
* 4 top and bottom layers
* 3 perimeters

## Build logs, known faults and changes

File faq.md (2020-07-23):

# Frequently Asked Questions

### How precise is it?
> Precision is a factor to how rigid the frame is, and how tight everything fits. Yes, you could get +/- .5 mm accuracy based on how well your components connect together and how rigid everything is overall. Remember, you're cutting wood, not sending something to the moon (well, maybe you are).

### How fast can it cut?
> Folks who have built it have stated an average range of 80-100 ipm (inches per minute) with 4mm deep cuts.

### What materials can it cut?
> Depending on the type of cutting bit, spindle RPMs, and cutting speed, you can cut a variety of materials, from plywood, MDF, solid wood, acrylic, form, and even aluminum

### How deep can it cut?
> If you use the printable parts, expect to get 2-1/2" - 3" max depth of cutting. If you use the Open Builds upgrades, you could cut deeper. The deeper you go, the cutting head gets further away from the gantry and you start to incorporate flex, which sacrifices accuracy.

### Can I attach something other than a router?
> Sure, with the proper printed gantry adapters you could connect virtually anything to the system. Markers, lasers, etc...

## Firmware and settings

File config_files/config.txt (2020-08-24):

#arm_solution      corexy
grbl_mode    true
# NOTE Lines must not exceed 132 characters
## Robot module configurations : general handling of movement G-codes and slicing into moves
default_feed_rate                            5000             # Default rate ( mm/minute ) for G1/G2/G3 moves
default_seek_rate                            5000             # Default rate ( mm/minute ) for G0 moves
mm_per_arc_segment                           0.02              # Arcs are cut into segments ( lines ), this is the length for
                                                              # these segments.  Smaller values mean more resolution,
                                                              # higher values mean faster computation
#mm_per_line_segment                          5                # Lines can be cut into segments ( not usefull with cartesian
                                                              # coordinates robots ).

## Network settings
network.enable                               true             # enable the ethernet network services
network.webserver.enable                     true             # enable the webserver
network.telnet.enable                        true             # enable the telnet server
network.ip_address                           192.168.1.111    # the IP address
network.ip_mask                              255.255.255.0    # the ip mask
network.ip_gateway                           192.168.1.1      # the gateway address
#network.mac_override                         45.E2.F9.4E.BD.49  # override the mac address, only do this if you have a conflict

# Arm solution configuration : Cartesian robot. Translates mm positions into stepper positions
alpha_steps_per_mm                           160 #200               # Steps per mm for alpha stepper
beta_steps_per_mm                            160 #160               # Steps per mm for beta stepper
gamma_steps_per_mm                           1600 #4535.44          # Steps per mm for gamma stepper

# Planner module configuration : Look-ahead and acceleration configuration
# See http://smoothieware.org/motion-control
acceleration                                 50 		# Acceleration in mm/second/second.
z_acceleration                               25 		# Acceleration for Z only moves in mm/s^2, 0 uses acceleration which is the default. DO NOT SET ON A DELTA
junction_deviation                           0.005              # See http://smoothieware.org/motion-control#junction-deviation
#z_junction_deviation                        0.0                # For Z only moves, -1 uses junction_deviation, zero disables junction_deviation on z moves DO NOT SET ON A DELTA

# Stepper module configuration
microseconds_per_step_pulse                  2                # Duration of step pulses to stepper drivers, in microseconds
base_stepping_frequency                      100000           # Base frequency for stepping

# Cartesian axis speed limits
x_axis_max_speed                             7000            # mm/min
y_axis_max_speed                             7000            # mm/min
z_axis_max_speed                             1200              # mm/min

# Stepper module pins ( ports, and pin numbers, appending "!" to the number will invert a pin )
alpha_step_pin                               2.0              # Pin for alpha stepper step signal
alpha_dir_pin                                0.5              # Pin for alpha stepper direction
alpha_en_pin                                 0.4              # Pin for alpha enable pin
alpha_current                                0.5             # X stepper motor current
alpha_max_rate                               7000.0          # mm/min

beta_step_pin                                2.1              # Pin for beta stepper step signal
beta_dir_pin                                 0.11!             # Pin for beta stepper direction
beta_en_pin                                  0.10             # Pin for beta enable
beta_current                                 0.5           # Y stepper motor current
beta_max_rate                                7000.0          # mm/min

gamma_step_pin                               2.2              # Pin for gamma stepper step signal
gamma_dir_pin                                0.20             # Pin for gamma stepper direction
gamma_en_pin                                 0.19             # Pin for gamma enable
gamma_current                                0.5              # Z stepper motor current
gamma_max_rate                               500.0            # mm/min

## System configuration
# Serial communications configuration ( baud rate defaults to 9600 if undefined )
uart0.baud_rate                              115200           # Baud rate for the default hardware serial port
second_usb_serial_enable                     true            # This enables a second usb serial port (to have both pronterface
                                                              # and a terminal connected)
#leds_disable                                true             # disable using leds after config loaded
#play_led_disable                            true             # disable the play led

# Kill button (used to be called pause) maybe assigned to a different pin, set to the onboard pin by default
kill_button_enable                           true             # set to true to enable a kill button
kill_button_pin                              2.12             # kill button pin. default is same as pause button 2.12 (2.11 is another good choice)

#msd_disable                                 false            # disable the MSD (USB SDCARD) when set to true (needs special binary)
#dfu_enable                                  false            # for linux developers, set to true to enable DFU
#watchdog_timeout                            10               # watchdog timeout in seconds, default is 10, set to 0 to disable the watchdog

# Only needed on a smoothieboard
currentcontrol_module_enable                 true             #

#extruder.hotend.x_offset                        0                # x offset from origin in mm
#extruder.hotend.y_offset                        0                # y offset from origin in mm
#extruder.hotend.z_offset                        0                # z offset from origin in mm

# firmware retract settings when using G10/G11, these are the defaults if not defined, must be defined for each extruder if not using the defaults
#extruder.hotend.retract_length                  3               # retract length in mm
#extruder.hotend.retract_feedrate                45              # retract feedrate in mm/sec
#extruder.hotend.retract_recover_length          0               # additional length for recover
#extruder.hotend.retract_recover_feedrate        8               # recover feedrate in mm/sec (should be less than retract feedrate)
#extruder.hotend.retract_zlift_length            0               # zlift on retract in mm, 0 disables
#extruder.hotend.retract_zlift_feedrate          6000            # zlift feedrate in mm/min (Note mm/min NOT mm/sec)

delta_current                                1.0              # First extruder stepper motor current

# Second extruder module configuration
#extruder.hotend2.enable                          true             # Whether to activate the extruder module at all. All configuration is ignored if false
#extruder.hotend2.steps_per_mm                    150              # Steps per mm for extruder stepper
#extruder.hotend2.default_feed_rate               600              # Default rate ( mm/minute ) for moves where only the extruder moves
#extruder.hotend2.acceleration                    500              # Acceleration for the stepper motor, as of 0.6, arbitrary ratio
#extruder.hotend2.max_speed                       50               # mm/s

#extruder.hotend2.step_pin                        2.8              # Pin for extruder step signal
#extruder.hotend2.dir_pin                         2.13             # Pin for extruder dir signal
#extruder.hotend2.en_pin                          4.29             # Pin for extruder enable signal

#extruder.hotend2.x_offset                        0                # x offset from origin in mm
#extruder.hotend2.y_offset                        25.0             # y offset from origin in mm
#extruder.hotend2.z_offset                        0                # z offset from origin in mm
epsilon_current                              1.0              # Second extruder stepper motor current
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

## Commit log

2020-07-23 Added amazon links for spindles
2020-07-23 Added OpenBuilds site reverence, and adtl spindles
    [zAxis_65mm_spindle.stl]
2020-07-27 updated bolts
2020-07-27 linked to adding rails
2020-07-27 added gantry pics
2020-07-27 questioning bolts
2020-08-05 Disabled Network
    [config.txt]
2020-08-05 changed spindle to pwm
    [config.txt]
2020-08-05 fixed spindle control
    [config.txt]
2020-08-06 re-enabled networking
    [config.txt]
2020-08-06 changed steps per mm
    [config.txt]
2020-08-06 changed stepper currents
    [config.txt]
2020-08-06 disabled temperature hotends
    [config.txt]
2020-08-06 disabled temperature control of bed
    [config.txt]
2020-08-06 Fixed network and leadscrew steps
    [config.txt]
2020-08-07 Replaced motion-control section
    Set junction deviation for standard CNC settings
    [config.txt]
2020-08-07 Clarified stepper module defaults
    [config.txt]
2020-08-07 fixed z-axis steps per rev
    [config.txt]
2020-08-10 Changed leadscrew to correct type with Amazon link
2020-08-11 Add files via upload
    running config
    [config.txt]
2020-08-14 Fixed z-axis steps per mm
    [config.txt]
